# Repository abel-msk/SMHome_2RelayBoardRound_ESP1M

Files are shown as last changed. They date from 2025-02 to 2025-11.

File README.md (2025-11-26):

# SMHome_UniversalRound_ESP32_C3_Mini
PCB designed board for smart home curtain controll, garage doors or any other equipment with two direction motor
with max power 220v 10A.

Board has ESP-8266 (ESP1M form factor)  two relays and  poweer convertor& 

Main goal of this pcb board is to place  it under wall mounted electric components in socket box, 
but of cource it steel can bee plcad in its own box.

## Haw to use

```
git clone https://github.com/abel-msk/SMHome_2RelayBoardRound_ESP1M
cd SMHome_UniversalRound_ESP32_C3_Mini
```
Next step is to open project file  `SMHome_2RelayBoardRound_ESP1M_v7.kicad_pro`  in KiKad. 

All footprint aggregated in local library `Library.pretty`, shematic symbols in `Library.kicad_sym`. You can add path to this library in project settings.

## 3D view on top of board

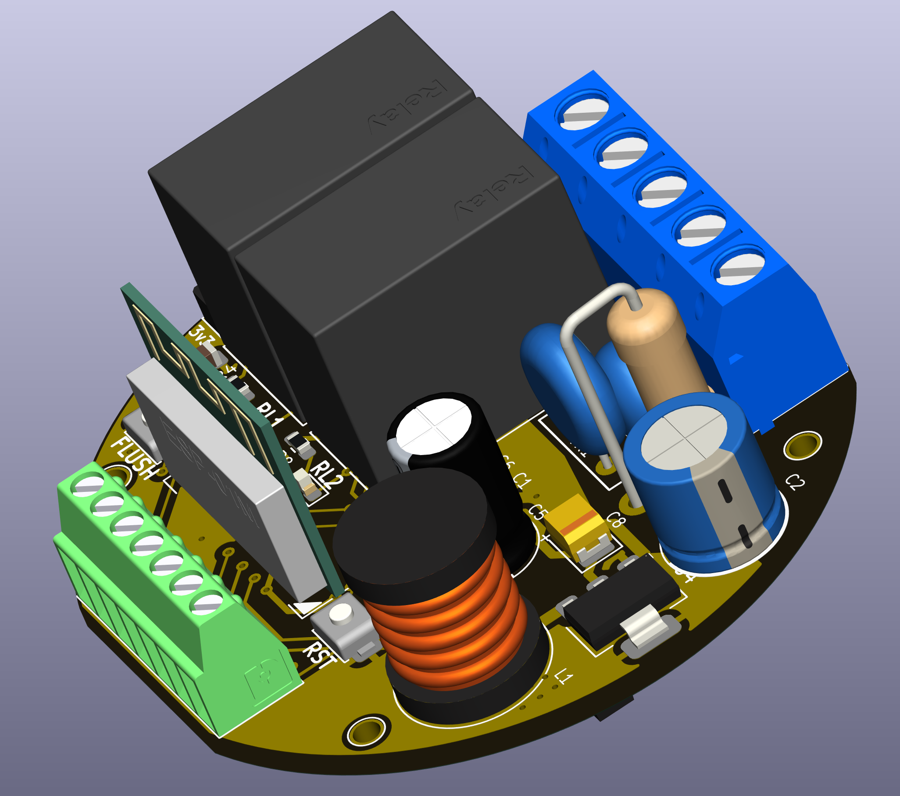
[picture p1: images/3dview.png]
3dview


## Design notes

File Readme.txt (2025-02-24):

Финальная версия платы с ESP-01M.   Вертикальная плата  с ESP-8266
Поправлено подключение РЕЛЕ 2 к новому пину.

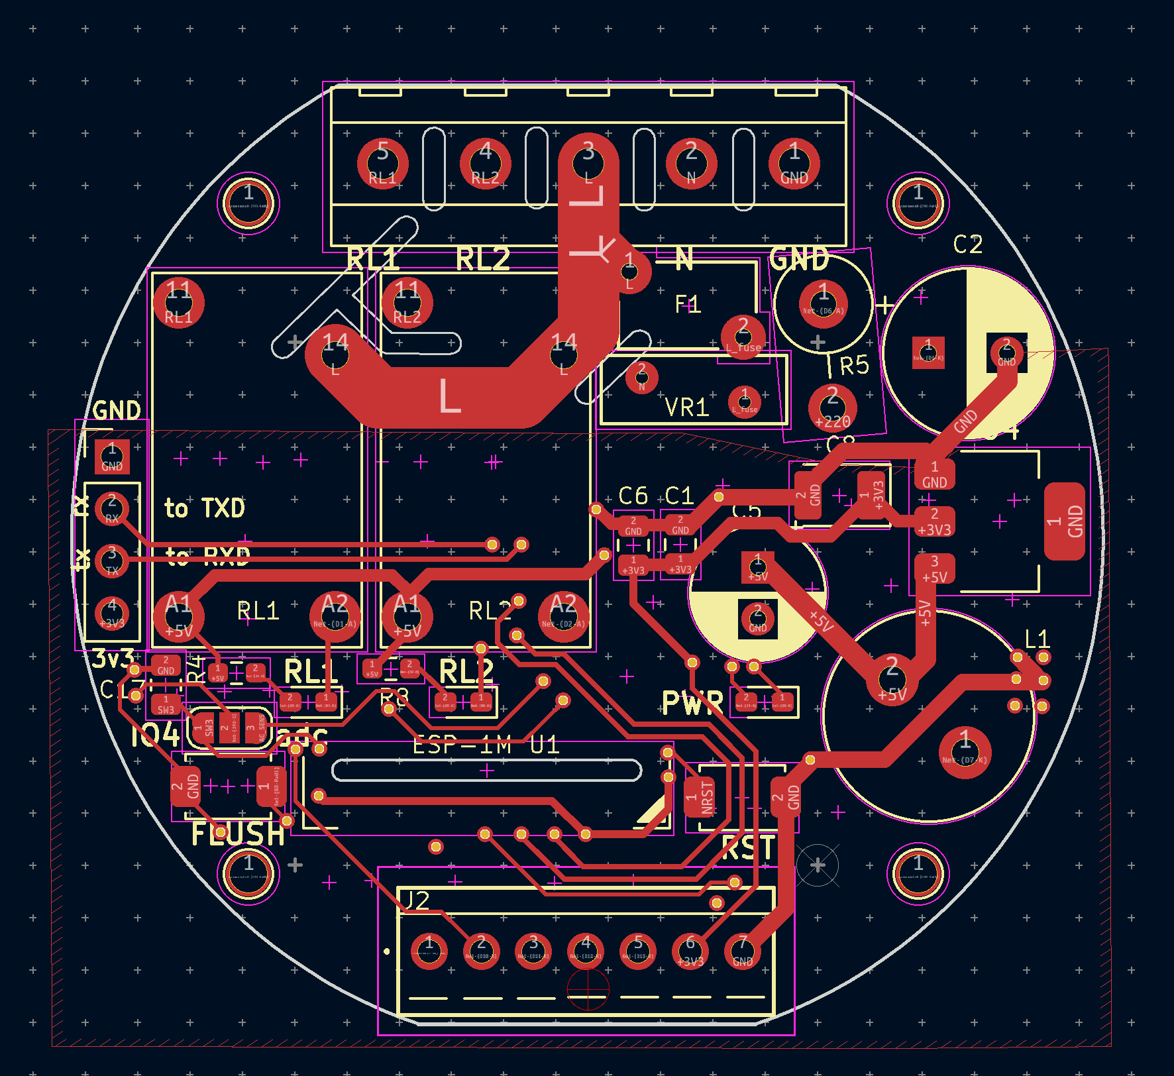
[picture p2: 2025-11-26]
images/top.png

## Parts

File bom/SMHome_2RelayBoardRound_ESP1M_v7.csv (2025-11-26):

# | Reference | Qty | Value | Footprint | comments | DNP | descr | Description
1 | B1,B2 | 2 | Button | Button_switch_SMD_Local:SW_Push_SPST_NO_Alps_SKRK_HandSoldering | SMD Btn 3*4*2 мм
2 | C2 | 1 | 4,7uF | Capacitor_THT:CP_Radial_D8.0mm_P3.80mm | 400v |  |  | 400v
3 | C5 | 1 | 680uF | Capacitor_THT:CP_Radial_D6.3mm_P2.50mm | 10v
4 | C7 | 1 | 4,7uF | Capacitor_SMD:C_0805_2012Metric_Pad1.18x1.45mm_HandSolder | 10v
5 | C8 | 1 | 10uF | Capacitor_Tantalum_SMD:CP_EIA-3528-21_Kemet-B | 6v; Tantalum SMD B
6 | C1,C4,C6,C10,C11,C14,C15,C16,C17 | 9 | 100nF | Capacitor_SMD:C_0805_2012Metric | 6v
7 | C3,C9 | 2 | 1uF | Capacitor_SMD:C_0805_2012Metric_Pad1.18x1.45mm_HandSolder | 10v
8 | D3 | 1 | blue_led | LED_SMD:LED_0603_1608Metric_Pad1.05x0.95mm_HandSolder
9 | D7 | 1 | ES1J | Diode_SMD:D_SMA |  |  |  | tr=35ns
10 | D8 | 1 | E1J | Diode_SMD:D_SOD-123F |  |  |  | tr<500ns; 1A; 600v
11 | D1,D2,D6 | 3 | 1N4007W (A7) | Diode_SMD:D_SOD-123F
12 | D4,D5 | 2 | green_led | LED_SMD:LED_0603_1608Metric_Pad1.05x0.95mm_HandSolder
13 | D9,D10,D11,D12,D13 | 5 | PESD3V3L1BA | Diode_SMD:D_SOD-323_HandSoldering
14 | DB1 | 1 | MB8S | Diode_local:MBS | D_Bridge_+-AA |  |  | D_Bridge_+-AA
15 | F1 | 1 | 250v/0.12A | Fuse_Local:RF145_D6.5mm_W4mm | RF146 |  | DNP
16 | J2 | 1 | K128_P7 | Connector_Phoenix_MPT:Phoenix Contact_MPT-0,5_7_2,54_P7 | KF128; Srew connector |  | DNP
17 | J3 | 1 | PinHead | Connector_PinHeader_2.54mm:PinHeader_1x04_P2.54mm_Vertical |  |  | DNP | Dupont 2.54 male
18 | J4 | 1 | 220V | TerminalBlock_Degson:DG301-5.0-05P |  |  | DG301-5.0-05P
19 | JP3 | 1 | jmp3 | Jumper:SolderJumper-3_P1.3mm_Open_RoundedPad1.0x1.5mm_NumberLabels |  |  | DNP
20 | L1 | 1 | 320uH | Inductor_THT:L_Radial_D10.0mm_P5.00mm_Fastron_07P |  |  | DNP
21 | Q1,Q2 | 2 | BC817 | Package_TO_SOT_SMD:SOT-23
22 | R5 | 1 | 10 | Resistor_THT:R_Axial_DIN0414_L11.9mm_D4.5mm_P5.08mm_Vertical | 1w |  | 1w
23 | R14 | 1 | 0,3 | Resistor_SMD:R_1206_3216Metric_Pad1.30x1.75mm_HandSolder | 1206 |  | 1206
24 | R26 | 1 | 40,2R | Resistor_SMD:R_0603_1608Metric_Pad0.98x0.95mm_HandSolder | Tolerance 0,1%
25 | R1,R6,R9 | 3 | 10K | Resistor_SMD:R_0603_1608Metric_Pad0.98x0.95mm_HandSolder
26 | R11,R12,R13,R15,R19,R27 | 6 | 100R | Resistor_SMD:R_0603_1608Metric_Pad0.98x0.95mm_HandSolder
27 | R2,R3,R4,R7,R8,R10 | 6 | 1k | Resistor_SMD:R_0603_1608Metric_Pad0.98x0.95mm_HandSolder
28 | RL1,RL2 | 2 | RJ-SS-105DM1 | Relay_THT_Local:RJ-SS-105DM1 |  |  | DNP | Wangrong Micro relay DIP reed relay, SPST, 5A, 220V
29 | TP2,TP3,TP4,TP5 | 4 | TestPoint | TestPoint:TestPoint_THTPad_D2.0mm_Drill1.0mm |  |  | DNP
30 | U1 | 1 | ESP-01M | WIFI_Module:ESP-01M |  |  | DNP
31 | U2 | 1 | BP2525F | Package_SO_Local:SOT33-5
32 | U4 | 1 | AMS1117-3.3 | Package_TO_SOT_SMD:SOT-223-3_TabPin2
33 | VR1 | 1 | 07D471K | Varistor:RV_Disc_D9mm_W3.3mm_P5mm | 07D471K; 300V |  | DNP

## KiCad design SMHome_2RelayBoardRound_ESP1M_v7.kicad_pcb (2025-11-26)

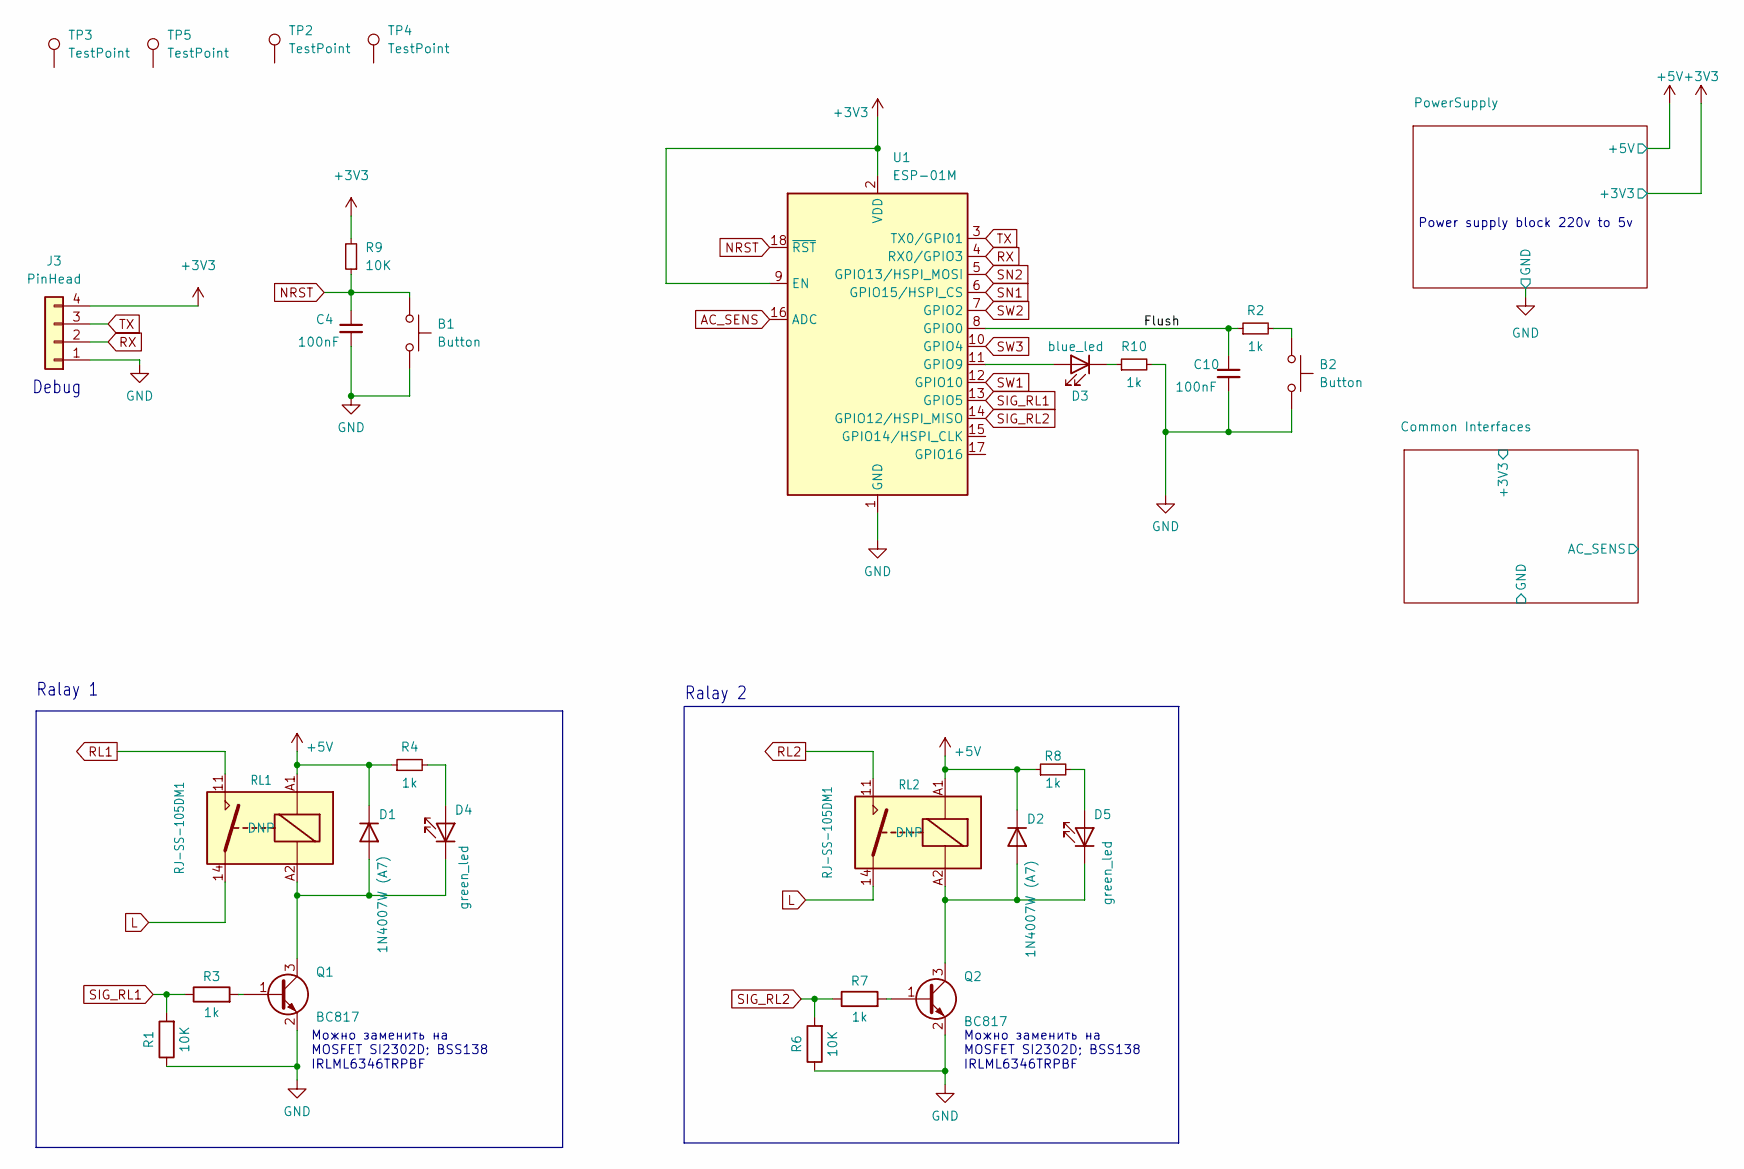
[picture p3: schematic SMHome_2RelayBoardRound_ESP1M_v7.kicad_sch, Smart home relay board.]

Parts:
B1, B2: Button; SW_Push_SPST_NO_Alps_SKRK_HandSoldering
C4, C10: 100nF; C_0805_2012Metric
D1, D2: 1N4007W (A7); D_SOD-123F
D3: blue_led; LED_0603_1608Metric_Pad1.05x0.95mm_HandSolder
D4, D5: green_led; LED_0603_1608Metric_Pad1.05x0.95mm_HandSolder
J3: PinHead; PinHeader_1x04_P2.54mm_Vertical
Q1, Q2: BC817; SOT-23
R1, R6, R9: 10K; R_0603_1608Metric_Pad0.98x0.95mm_HandSolder
R2, R3, R4, R7, R8, R10: 1k; R_0603_1608Metric_Pad0.98x0.95mm_HandSolder
RL1, RL2: RJ-SS-105DM1
TP2, TP3, TP4, TP5: TestPoint; TestPoint_THTPad_D2.0mm_Drill1.0mm
U1: ESP-01M

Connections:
+3V3: J3.4, R9.2, U1.2 (VDD), U1.9 (EN); also elsewhere on the board
+5V: D1.1 (K), D2.1 (K), R4.1, R8.1, RL1.A1, RL2.A1; also elsewhere on the board
/Flush: C10.1, R2.1, U1.8 (GPIO0)
AC_SENS: U1.16 (ADC); also elsewhere on the board
GND: B1.2, B2.2, C4.2, C10.2, J3.1, Q1.2 (E), Q2.2 (E), R1.1, R6.1, R10.2, U1.1 (GND); also elsewhere on the board
L: RL1.14, RL2.14; also elsewhere on the board
NRST: B1.1, C4.1, R9.1, U1.18 (~RST)
unnamed: B2.1, R2.2
unnamed: D1.2 (A), D4.1 (K), Q1.3 (C), RL1.A2
unnamed: D2.2 (A), D5.1 (K), Q2.3 (C), RL2.A2
unnamed: D3.2 (A), U1.11 (GPIO9)
unnamed: D3.1 (K), R10.1
unnamed: D4.2 (A), R4.2
unnamed: D5.2 (A), R8.2
unnamed: Q1.1 (B), R3.2
unnamed: Q2.1 (B), R7.2
RL1: RL1.11; also elsewhere on the board
RL2: RL2.11; also elsewhere on the board
RX: J3.2, U1.4 (RX0/GPIO3)
SIG_RL1: R1.2, R3.1, U1.13 (GPIO5)
SIG_RL2: R6.2, R7.1, U1.14 (GPIO12/HSPI_MISO)
SN1: U1.6 (GPIO15/HSPI_CS); also elsewhere on the board
SN2: U1.5 (GPIO13/HSPI_MOSI); also elsewhere on the board
SW1: U1.12 (GPIO10); also elsewhere on the board
SW2: U1.7 (GPIO2); also elsewhere on the board
SW3: U1.10 (GPIO4); also elsewhere on the board
TX: J3.3, U1.3 (TX0/GPI01)

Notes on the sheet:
Power supply block 220v to 5v
Можно заменить на MOSFET SI2302D; BSS138 IRLML6346TRPBF
Debug
Ralay 2
Ralay 1

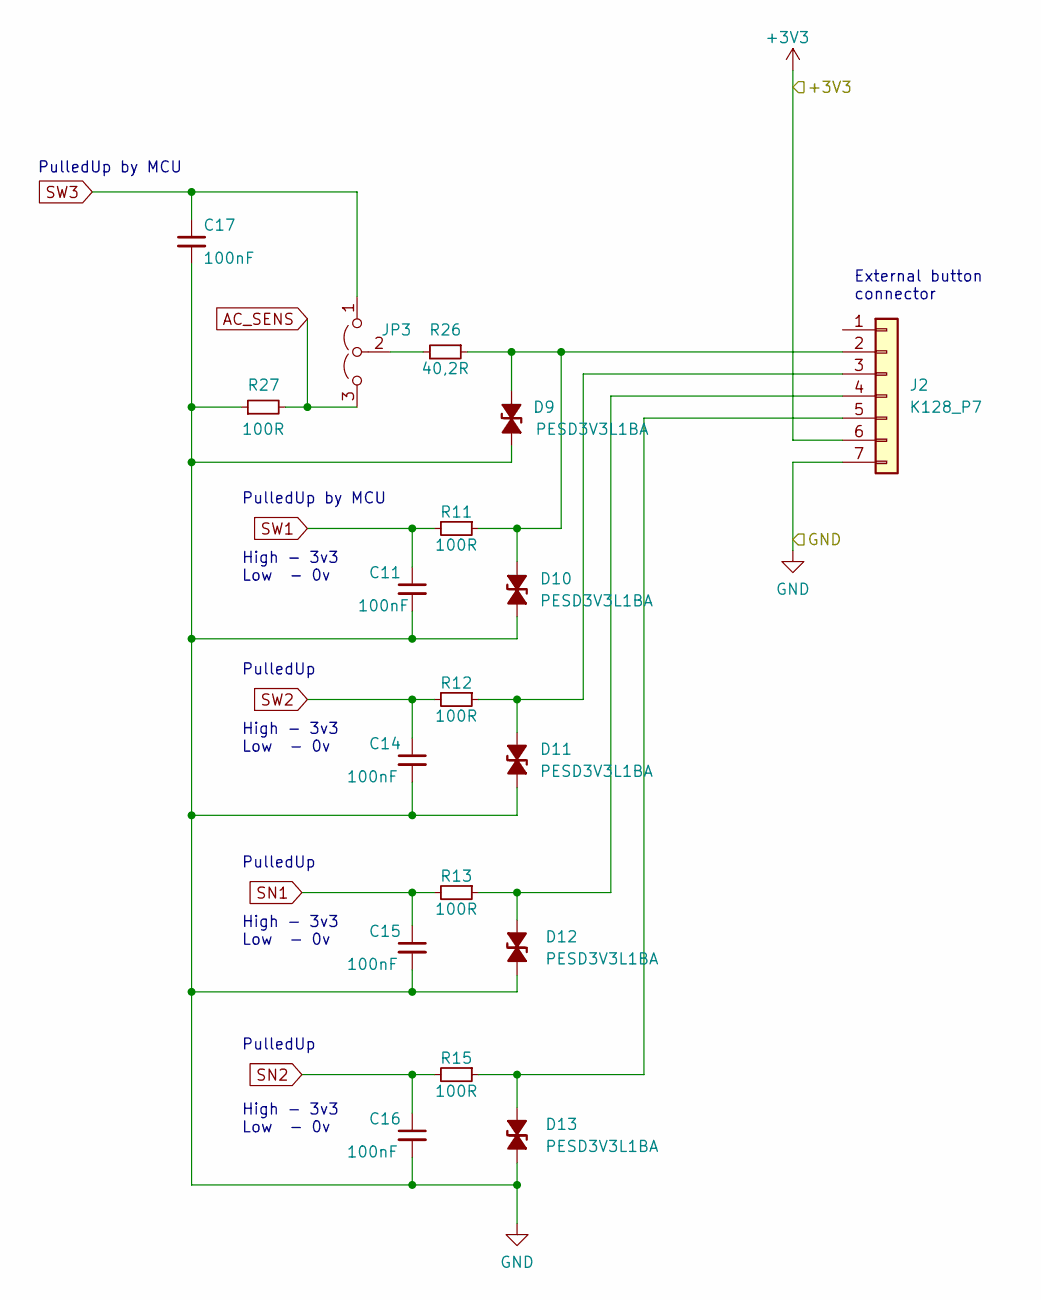
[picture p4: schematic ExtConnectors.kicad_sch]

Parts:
C11, C14, C15, C16, C17: 100nF; C_0805_2012Metric
D9, D10, D11, D12, D13: PESD3V3L1BA; D_SOD-323_HandSoldering
J2: K128_P7; Phoenix Contact_MPT-0,5_7_2,54_P7
JP3: jmp3; SolderJumper-3_P1.3mm_Open_RoundedPad1.0x1.5mm_NumberLabels
R11, R12, R13, R15, R27: 100R; R_0603_1608Metric_Pad0.98x0.95mm_HandSolder
R26: 40,2R; R_0603_1608Metric_Pad0.98x0.95mm_HandSolder

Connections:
+3V3: J2.6; also elsewhere on the board
AC_SENS: JP3.3 (B), R27.2; also elsewhere on the board
GND: C11.2, C14.2, C15.2, C16.2, C17.2, D9.1 (K), D10.1 (K), D11.2 (A), D12.2 (A), D13.2 (A), J2.7, R27.1; also elsewhere on the board
unnamed: D9.2 (A), D10.2 (A), J2.2, R11.1, R26.1
unnamed: D11.1 (K), J2.3, R12.1
unnamed: D12.1 (K), J2.4, R13.1
unnamed: D13.1 (K), J2.5, R15.1
unnamed: JP3.2 (C), R26.2
SN1: C15.1, R13.2; also elsewhere on the board
SN2: C16.1, R15.2; also elsewhere on the board
SW1: C11.1, R11.2; also elsewhere on the board
SW2: C14.1, R12.2; also elsewhere on the board
SW3: C17.1, JP3.1 (A); also elsewhere on the board

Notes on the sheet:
External button connector
PulledUp
PulledUp by MCU
High - 3v3 Low - 0v

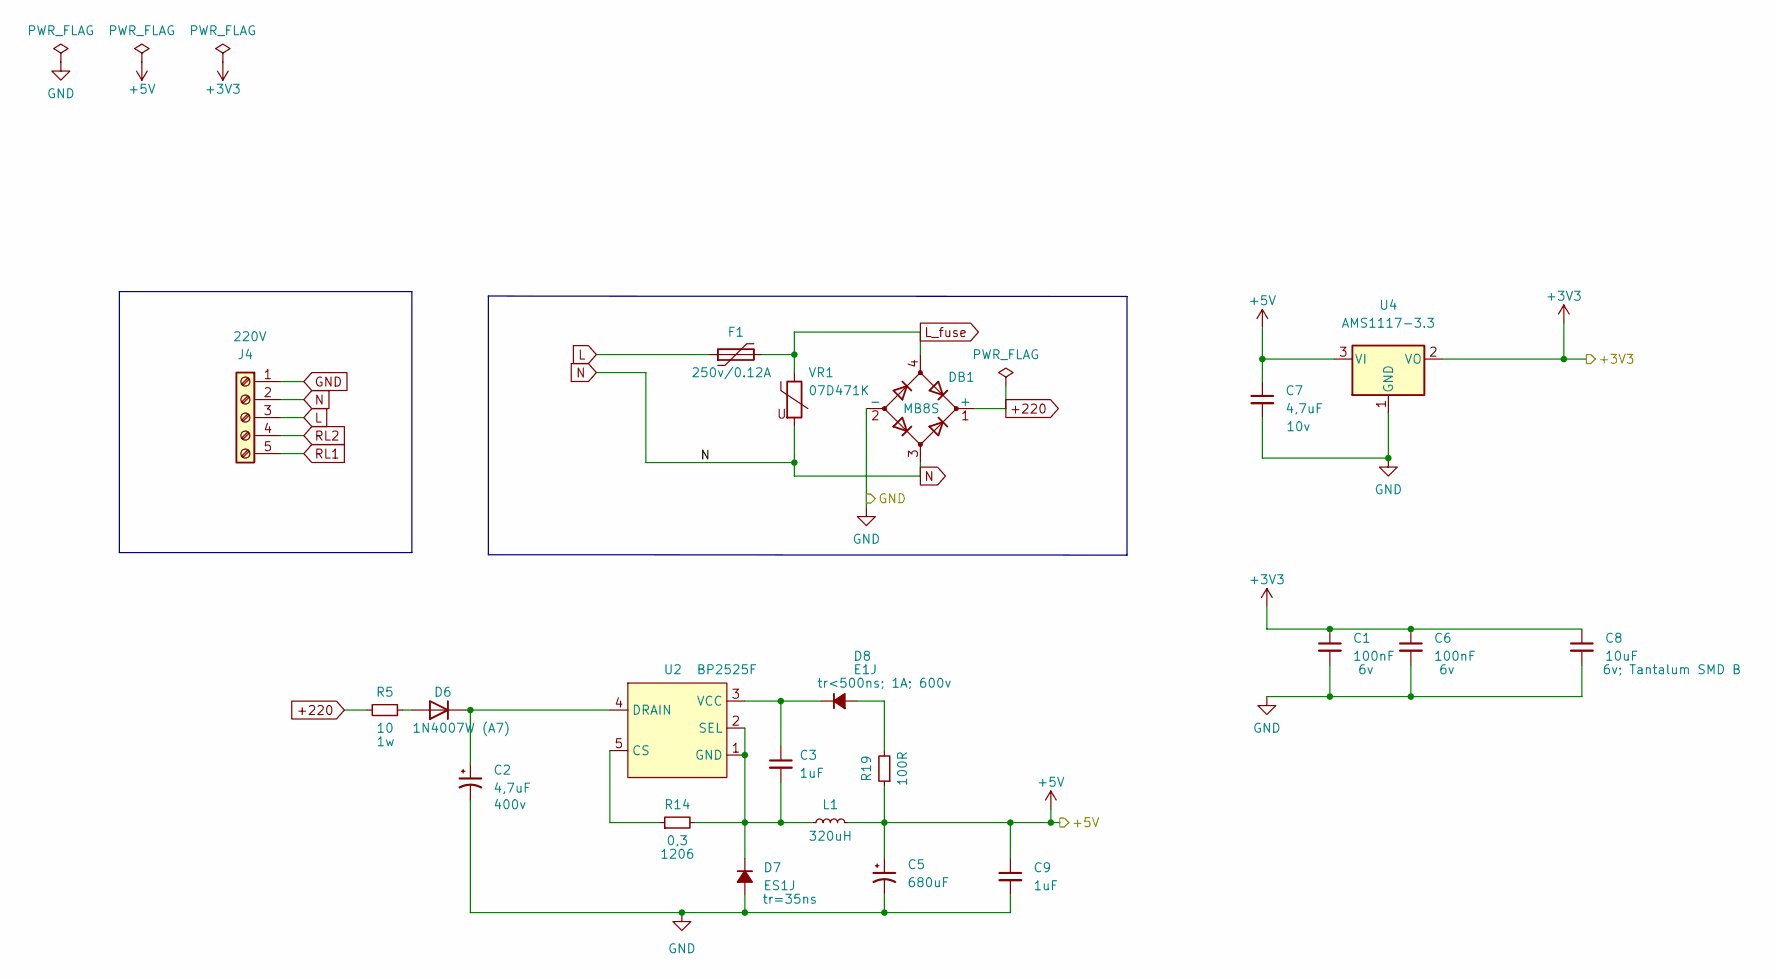
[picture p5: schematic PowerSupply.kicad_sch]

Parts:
C1, C6: 100nF; C_0805_2012Metric
C2: 4,7uF; CP_Radial_D8.0mm_P3.80mm
C3, C9: 1uF; C_0805_2012Metric_Pad1.18x1.45mm_HandSolder
C5: 680uF; CP_Radial_D6.3mm_P2.50mm
C7: 4,7uF; C_0805_2012Metric_Pad1.18x1.45mm_HandSolder
C8: 10uF; CP_EIA-3528-21_Kemet-B
D6: 1N4007W (A7); D_SOD-123F
D7: ES1J; D_SMA
D8: E1J; D_SOD-123F
DB1: MB8S; MBS
F1: 250v/0.12A; RF145_D6.5mm_W4mm
J4: 220V; DG301-5.0-05P
L1: 320uH; L_Radial_D10.0mm_P5.00mm_Fastron_07P
R5: 10; R_Axial_DIN0414_L11.9mm_D4.5mm_P5.08mm_Vertical
R14: 0,3; R_1206_3216Metric_Pad1.30x1.75mm_HandSolder
R19: 100R; R_0603_1608Metric_Pad0.98x0.95mm_HandSolder
U2: BP2525F; SOT33-5
U4: AMS1117-3.3; SOT-223-3_TabPin1
VR1: 07D471K; RV_Disc_D9mm_W3.3mm_P5mm

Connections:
+3V3: C1.1, C6.1, C8.1, U4.2 (VO); also elsewhere on the board
+5V: C5.1, C7.1, C9.1, L1.2, R19.1, U4.3 (VI); also elsewhere on the board
+220: DB1.1 (+), R5.2
GND: C1.2, C2.2, C5.2, C6.2, C7.2, C8.2, C9.2, D7.2 (A), DB1.2 (-), J4.1, U4.1 (GND); also elsewhere on the board
L: F1.1, J4.3; also elsewhere on the board
L_fuse: DB1.4, F1.2, VR1.1
N: DB1.3, J4.2, VR1.2
unnamed: D6.2 (A), R5.1
unnamed: C2.1, D6.1 (K), U2.4 (DRAIN)
unnamed: C3.2, D7.1 (K), L1.1, R14.2, U2.1 (GND), U2.2 (SEL)
unnamed: D8.2 (A), R19.2
unnamed: C3.1, D8.1 (K), U2.3 (VCC)
unnamed: R14.1, U2.5 (CS)
RL1: J4.5; also elsewhere on the board
RL2: J4.4; also elsewhere on the board

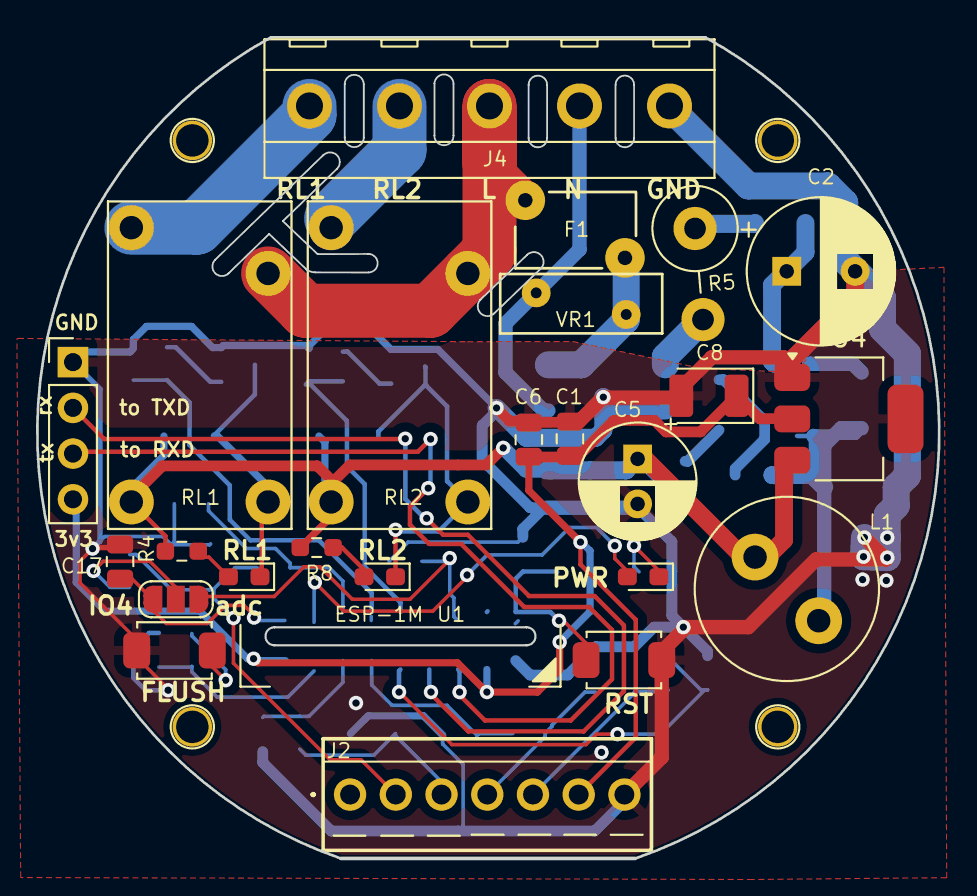
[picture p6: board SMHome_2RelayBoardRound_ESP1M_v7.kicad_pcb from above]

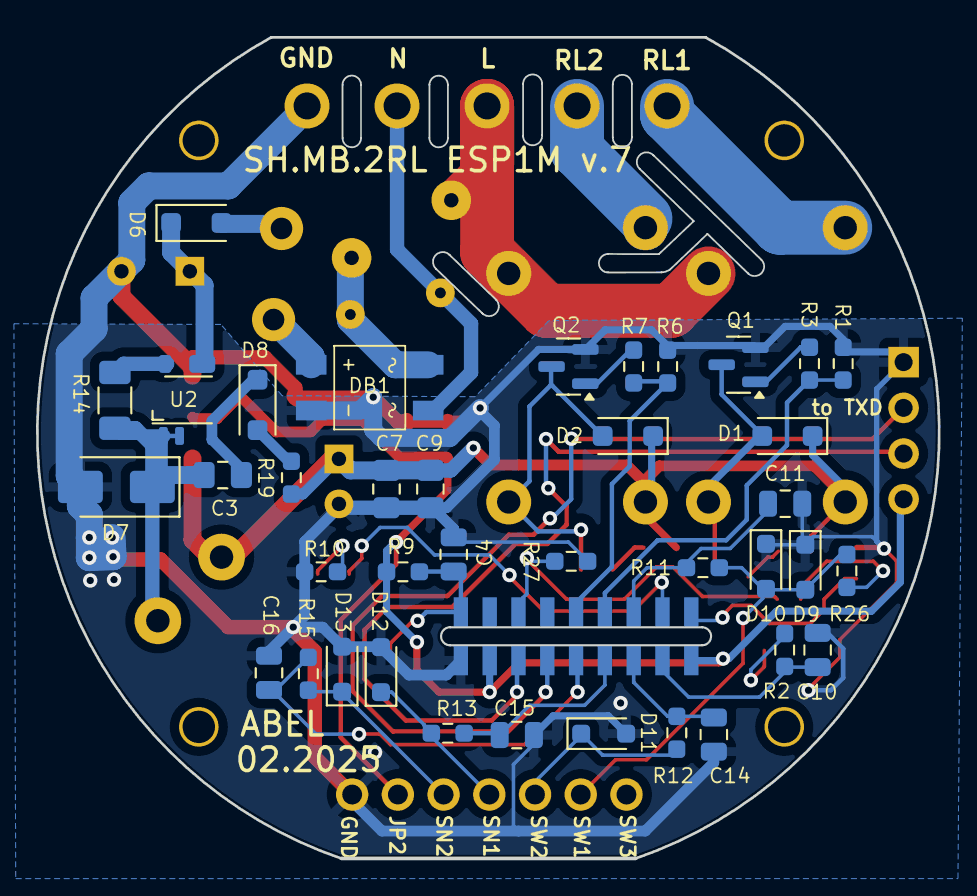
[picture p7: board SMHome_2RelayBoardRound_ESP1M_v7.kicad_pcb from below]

Board: 2 copper layers, 50.1 x 45.6 mm, 67 parts (38 on the bottom side), 41 nets.

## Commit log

2025-02-24 add gitignore
    [ExtConnectors.kicad_sch, MCU_STM32.kicad_sch, PowerSupply.kicad_sch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]
2025-11-26 Migrated to KiKad9
    [ExtConnectors.kicad_sch, PowerSupply.kicad_sch, SMHome_2RelayBoardRound_ESP1M_v7.csv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]
